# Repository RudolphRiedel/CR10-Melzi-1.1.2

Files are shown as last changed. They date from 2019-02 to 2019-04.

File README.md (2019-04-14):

This is a fork from https://github.com/Creality3DPrinting/CR10-Melzi-1.1.2

The files that Creality3D provided are neither the Source or Open and as a clone of the Melzi design which is under GPL Creality3D
should have released the real files over a year earlier than the subset that they released now.
Furthermore all Creality3D does is dumping the files on Github and not supporting them in any way.
All issues with the data seem to be ignored as well as any request.

Their supplied "CR-10 Schematic.pdf" does neither match the "CR-10 Motherboard.PCB" file,
nor is it the source-file but merely a picture.
For example, the controller is named U5 in the schematic but U8 in the board-file.
And the jumper J5 from the schematic to switch VCC between USB and the 5V regulator, it does not even exist
in the board-file.
Yes, there is an issue open for that: https://github.com/Creality3DPrinting/CR-10/issues/1

So, why the fuss, why this repository?
I still do care about the repairabilty of my CR-10 and Ender-3.

So I did my own version of the schematic from scratch based on the Ender-3.PCB in the Ender-3 repository.
This is my try to provide data for the V1.1.2 board as I believe Creality3D should have provided themselves when starting to sell the CR-10 at least.

This is a complete Altium Designer project now, saved with AD17.
Note: the "CR-10 Motherboard.PcbDoc" is not the same as "CR-10 Motherboard.PCB", it is based on that file but already
has a couple of bugfixes implemented. Not to change anything, but to correct the faulty patched mess of the "CR-10 Motherboard.PCB".

I would have loved to work on this together with Creality3D but I can only guess that they are not interested in really embracing open source. 

When I received my first Ender-3 it had a board installed in it with "V1.1.3" printed on the silkscreen.
I asked in the Ender-3 repository what changed from "V1.1.2" but got no answer to that quesion.

I am still not sure but I believe the only difference is that the header EXT-A2 has been replaced with a 100µF/16V capacitor.

The Ender-3 at least has been quietely been "upgraded" to a "V1.1.4" revision of the controller-board.
I only had pictures to work with but the only change that I found is that the FT232RL has been swapped out for a CH340G.
I find that is a bold move given that the USB chip provides the 3.3V for the SD-card and while the FT232RL is rated for 50mA, the CH340G does not even have a rating for the output current in the datasheet.
I would have added a small LDO for the 3.3V in addition but Creality3D did not.

I would not be surprised at all if this turns out to be a major cause for broken V1.1.4 boards.

Next thing I learned is that Creality3D started to offer a silent upgrade mainboard.
What they did is to replace the A4988 stepper drivers with TMC2208.
This is just a drop-in replacement and they did not change the board for it.
Also if you did receive your Ender-3 with a V1.1.4 board you likely have A4988 drivers installed.
Looking at a still from a Youtube video they changed the sense resistors from 0,1R to 0,15R.
C10, C14, C18 and C22 should have been changed to 22nF.

Original content of the README.md:

# CR10-Melzi-1.1.2
The CR10 Melzi 1.1.2 3D Printer Motherboard is now fully Open Source Hardware Association Certified.

UID:CN000004
https://certification.oshwa.org/list.html

Hardware and software licensed under the GPL v3 license, documentation licensed under CC BY-SA 4.0 International license.

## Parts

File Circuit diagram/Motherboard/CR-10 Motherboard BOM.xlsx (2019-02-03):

Quantity | Designator | Description | Comment | Footprint
1 | U2 | 74HC541 - Octal buffer/line driver | HC541 | SSOP-20
4 | U3, U4, U6, U7 | A4988 | A4988 | QFP28
1 | U8 | AVR 8-Bit, 128k FLASH, TQFP44 | ATMEGA1284P-AU | QFP-44
6 | C1, C2, C3, C4, C28, C30 | Capacitor Polarized | 100uF | CAP-100
1 | CP2 | Capacitor Polarized | 22uF | RVT4X5.5
1 | C45 | Chip Capacitor | 330nF | 0603
2 | C25, C40 | Chip Capacitor | 220nF | 0603
2 | C41, C42 | Chip Capacitor | 1uF | 0603
2 | C50, C51 | Chip Capacitor | 22p | 0603
25 | C10, C11, C12, C13, C14, C15, C16, C17, C18, C19, C20, C21, C22, C23, C24, C32, C33, C34, C35, C36, C37, C38, C39, C43, C44 | Chip Capacitor | 100nF | 0603
1 | C31 | Chip Capacitor | 100nF | 0805
5 | C5, C6, C7, C8, C9 | Chip Capacitor | 4.7uF | 0805
1 | CP1 | Chip Capacitor | 0.1uF | C0603
1 | CP3 | Chip Capacitor | 150pF | C0603
2 | R25, R26 | Chip Resistor | 1k | 0603
1 | 1k | Chip Resistor | R1-1 | 0603
12 | R18, R27, R28, R29, R30, R31, R32, R33, R34, R35, R36, R37 | Chip Resistor | 0R | 0603
16 | R1, R2, R3, R4, R5, R10, R11, R12, R14, R15, R17, R20, R21, R23, R24, R38 | Chip Resistor | 10k | 0603
4 | R13, R16, R19, R22 | Chip Resistor | 100k | 0603
4 | R6, R7, R8, R9 | Chip Resistor | 20k | 0603
1 | FP1 | Chip Resistor | 1.5A | MF-MSMF050
1 | R_P2 | Chip Resistor | 24.9k | R0603
1 | R_P4 | Chip Resistor | 210k | R0603
1 | R_P5 | Chip Resistor | 40.2k | R0603
3 | R_P1, R_P3, R_P6 | Chip Resistor | 100k | R0603
3 | JS1, JS2, JS3 | Chip Resistor | not populated | R10
8 | S1, S2, S3, S4, S5, S6, S7, S8 | Chip Resistor | 0.1R | R100
1 | 16M | Crystal HC49/US | 16Mhz | CRY
1 | DP1 | Diode | B340A-13-F | D-SMA
1 | DP2 | Diode | SS12 | D-SMA
3 | Fid1, Fid2, Fid3 | Fiducial | Fiducial | Fiducial-A
1 | U1 | FTDI USB UART I.C. | FT232RL | PL2303
7 | B-MOT, ETEMP, FAN, FAN1, X-STOP, Y-STOP, Z-STOP | Header 1x2 | XH2.54-2A | P2
1 | EXT-A2 | Header 1x3 | XH2.54-3A | XH-3A
4 | E-MOT, X-MOT, Y-MOT, Z-MOT | Header 1x4 | XH2.54-4A | P4
1 | ISP | Header 2x3 | HEADER 3X2
1 | EXP1 | Header 2x5 | Header 2x5 | SOP10
1 | LP1 | Inductor | 15uH/3A | DO3316P
2 | LED1, LED2 | LED | blue | 0603
1 | TF | microSD | TF | TF
1 | UP1 | MP1584 | MP1584 | SOIC8E
3 | M1, M2, M3 | N-FET | REP30N06LE | TO-252
4 | RP1, RP2, RP3, RP4 | RTrimm | 10k | RP
3 | Hotbed, Hotend, PWR | Terminal 1x2 | HP128-5.0-2P | MOT-2
1 | USB | USB | mini-USB | USB

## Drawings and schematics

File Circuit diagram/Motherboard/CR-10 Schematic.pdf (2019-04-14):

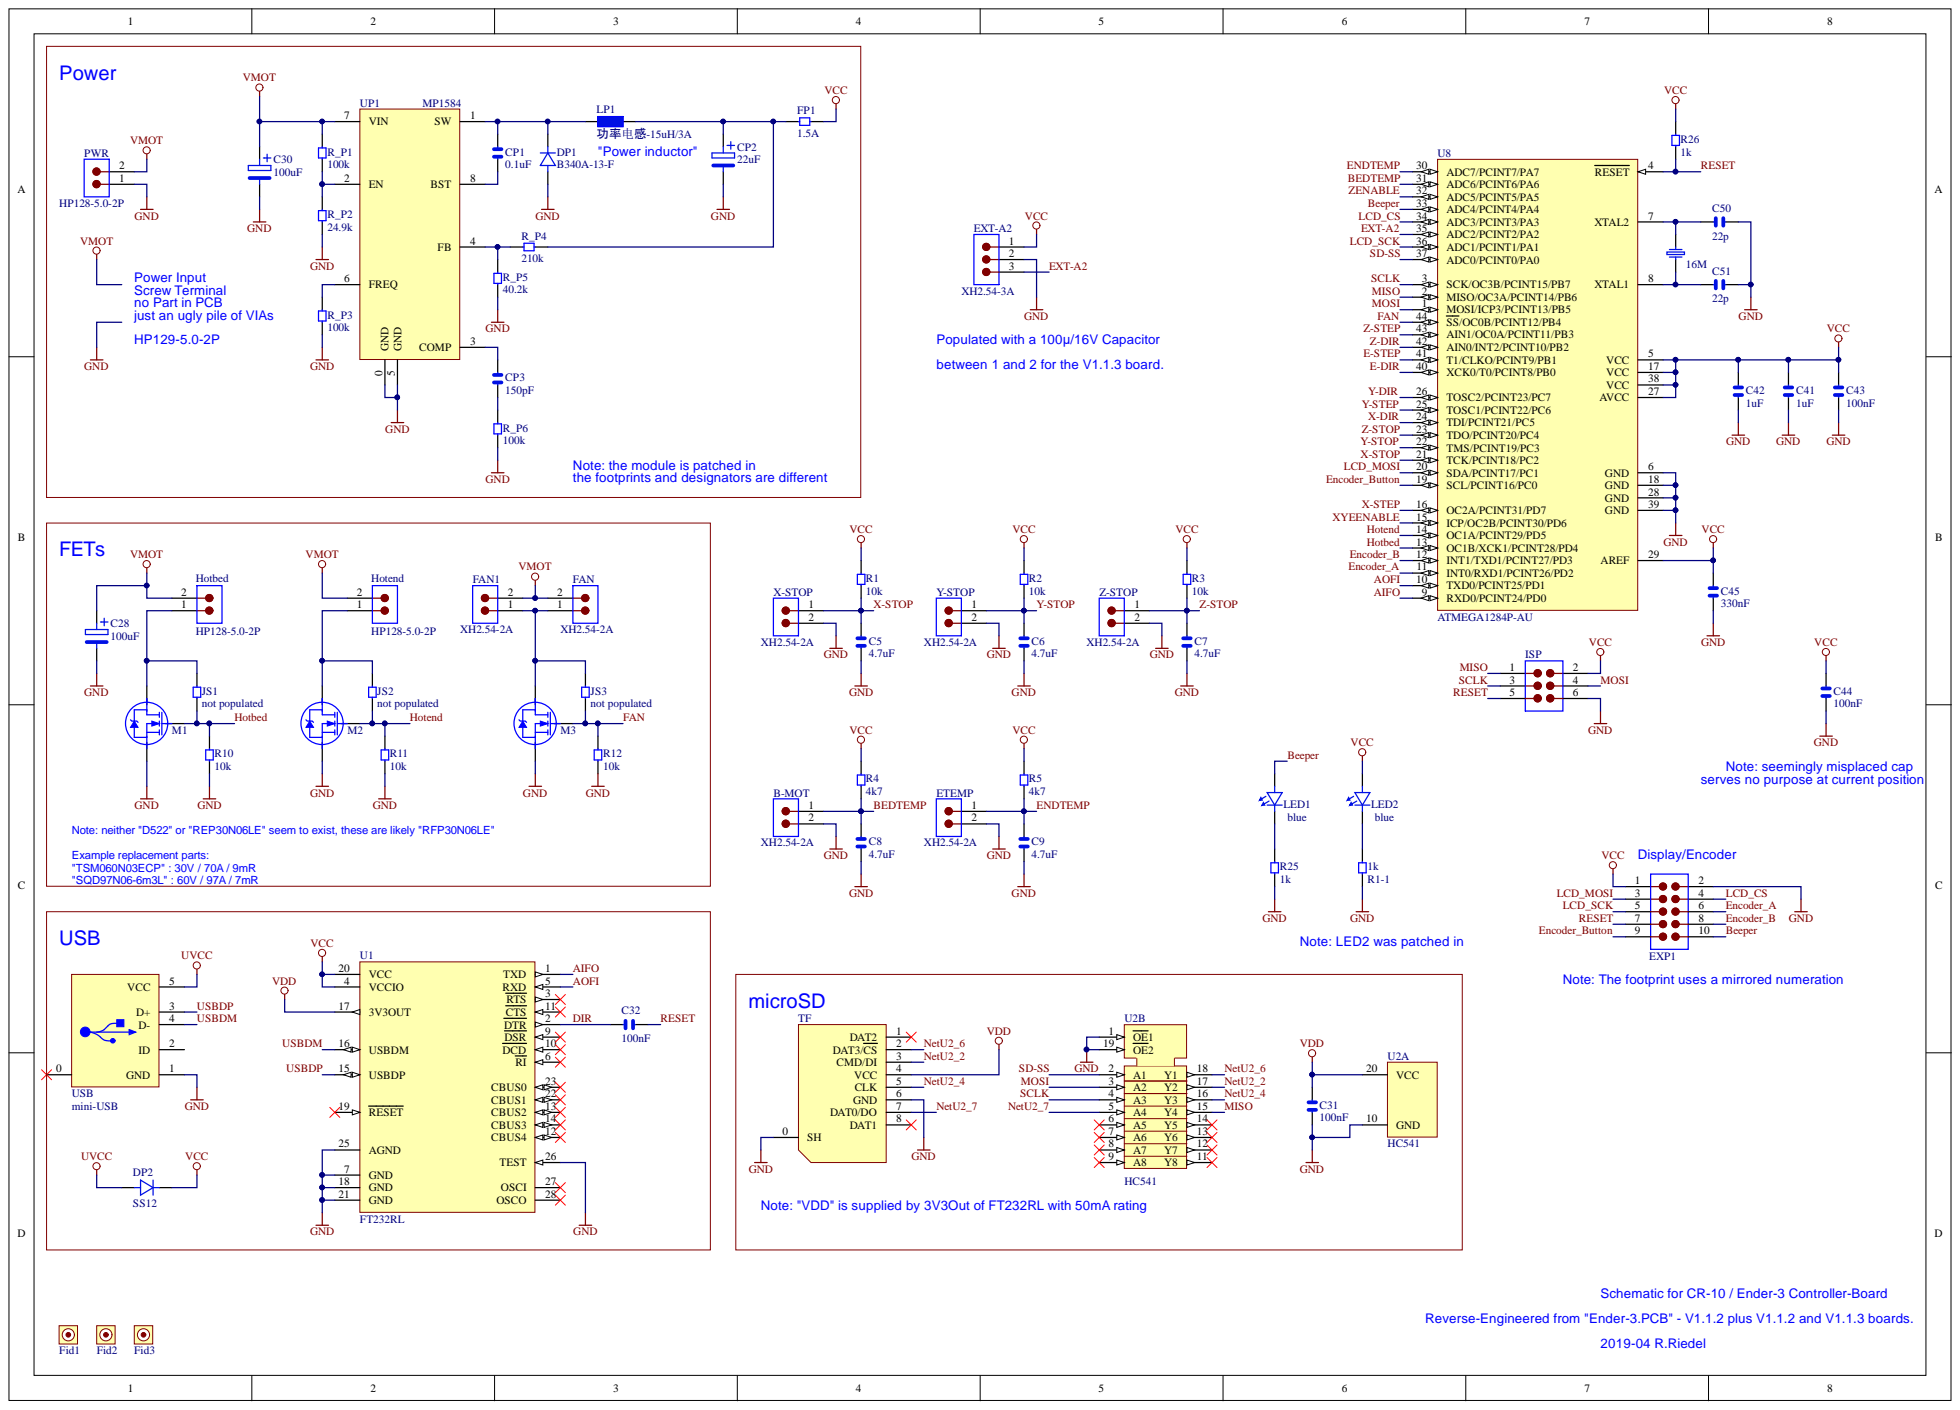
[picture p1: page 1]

Power Input
Screw Terminal no Part in PCB

just an ugly pile of VIAs

between 1 and 2 for the V1.1.3 board.

Note: the module is patched in
the footprints and designators are different

serves no purpose at current position Note: seemingly misplaced cap

Note: neither "D522" or "REP30N06LE" seem to exist, these are likely "RFP30N06LE"

GND
Note: LED2 was patched in

Note: The footprint uses a mirrored numeration

GND 7

GND 21

Note: "VDD" is supplied by 3V3Out of FT232RL with 50mA rating

Schematic for CR-10 / Ender-3 Controller-Board

Reverse-Engineered from "Ender-3.PCB" - V1.1.2 plus V1.1.2 and V1.1.3 boards.

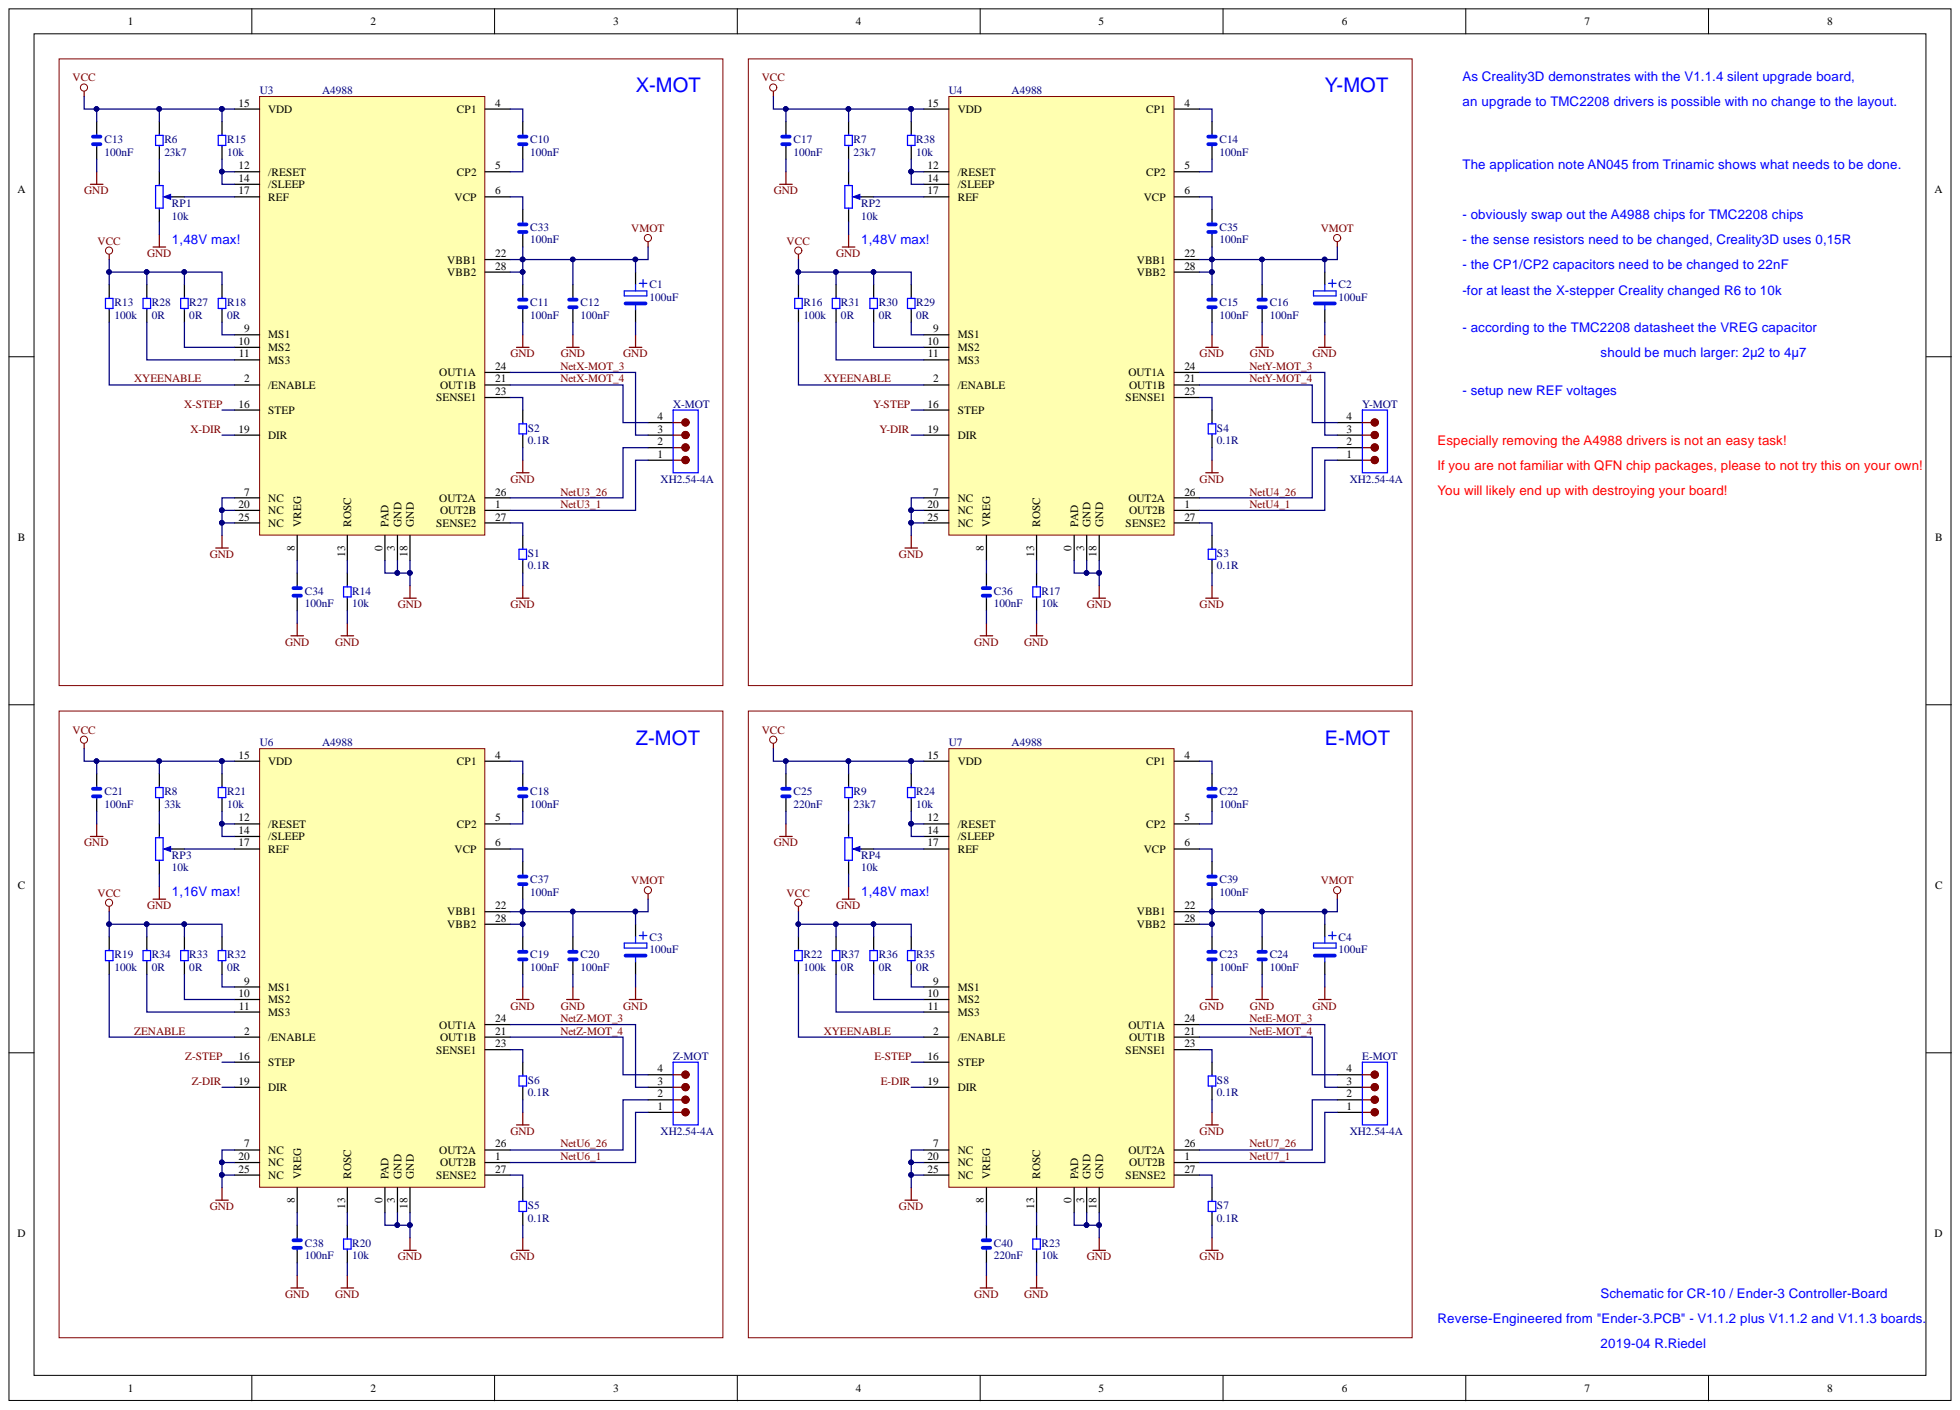
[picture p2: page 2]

As Creality3D demonstrates with the V1.1.4 silent upgrade board,

an upgrade to TMC2208 drivers is possible with no change to the layout.

The application note AN045 from Trinamic shows what needs to be done.

- obviously swap out the A4988 chips for TMC2208 chips

- the sense resistors need to be changed, Creality3D uses 0,15R

- the CP1/CP2 capacitors need to be changed to 22nF

-for at least the X-stepper Creality changed R6 to 10k

- according to the TMC2208 datasheet the VREG capacitor

should be much larger: 2µ2 to 4µ7

- setup new REF voltages

Especially removing the A4988 drivers is not an easy task!

If you are not familiar with QFN chip packages, please to not try this on your own!

You will likely end up with destroying your board!

Schematic for CR-10 / Ender-3 Controller-Board

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

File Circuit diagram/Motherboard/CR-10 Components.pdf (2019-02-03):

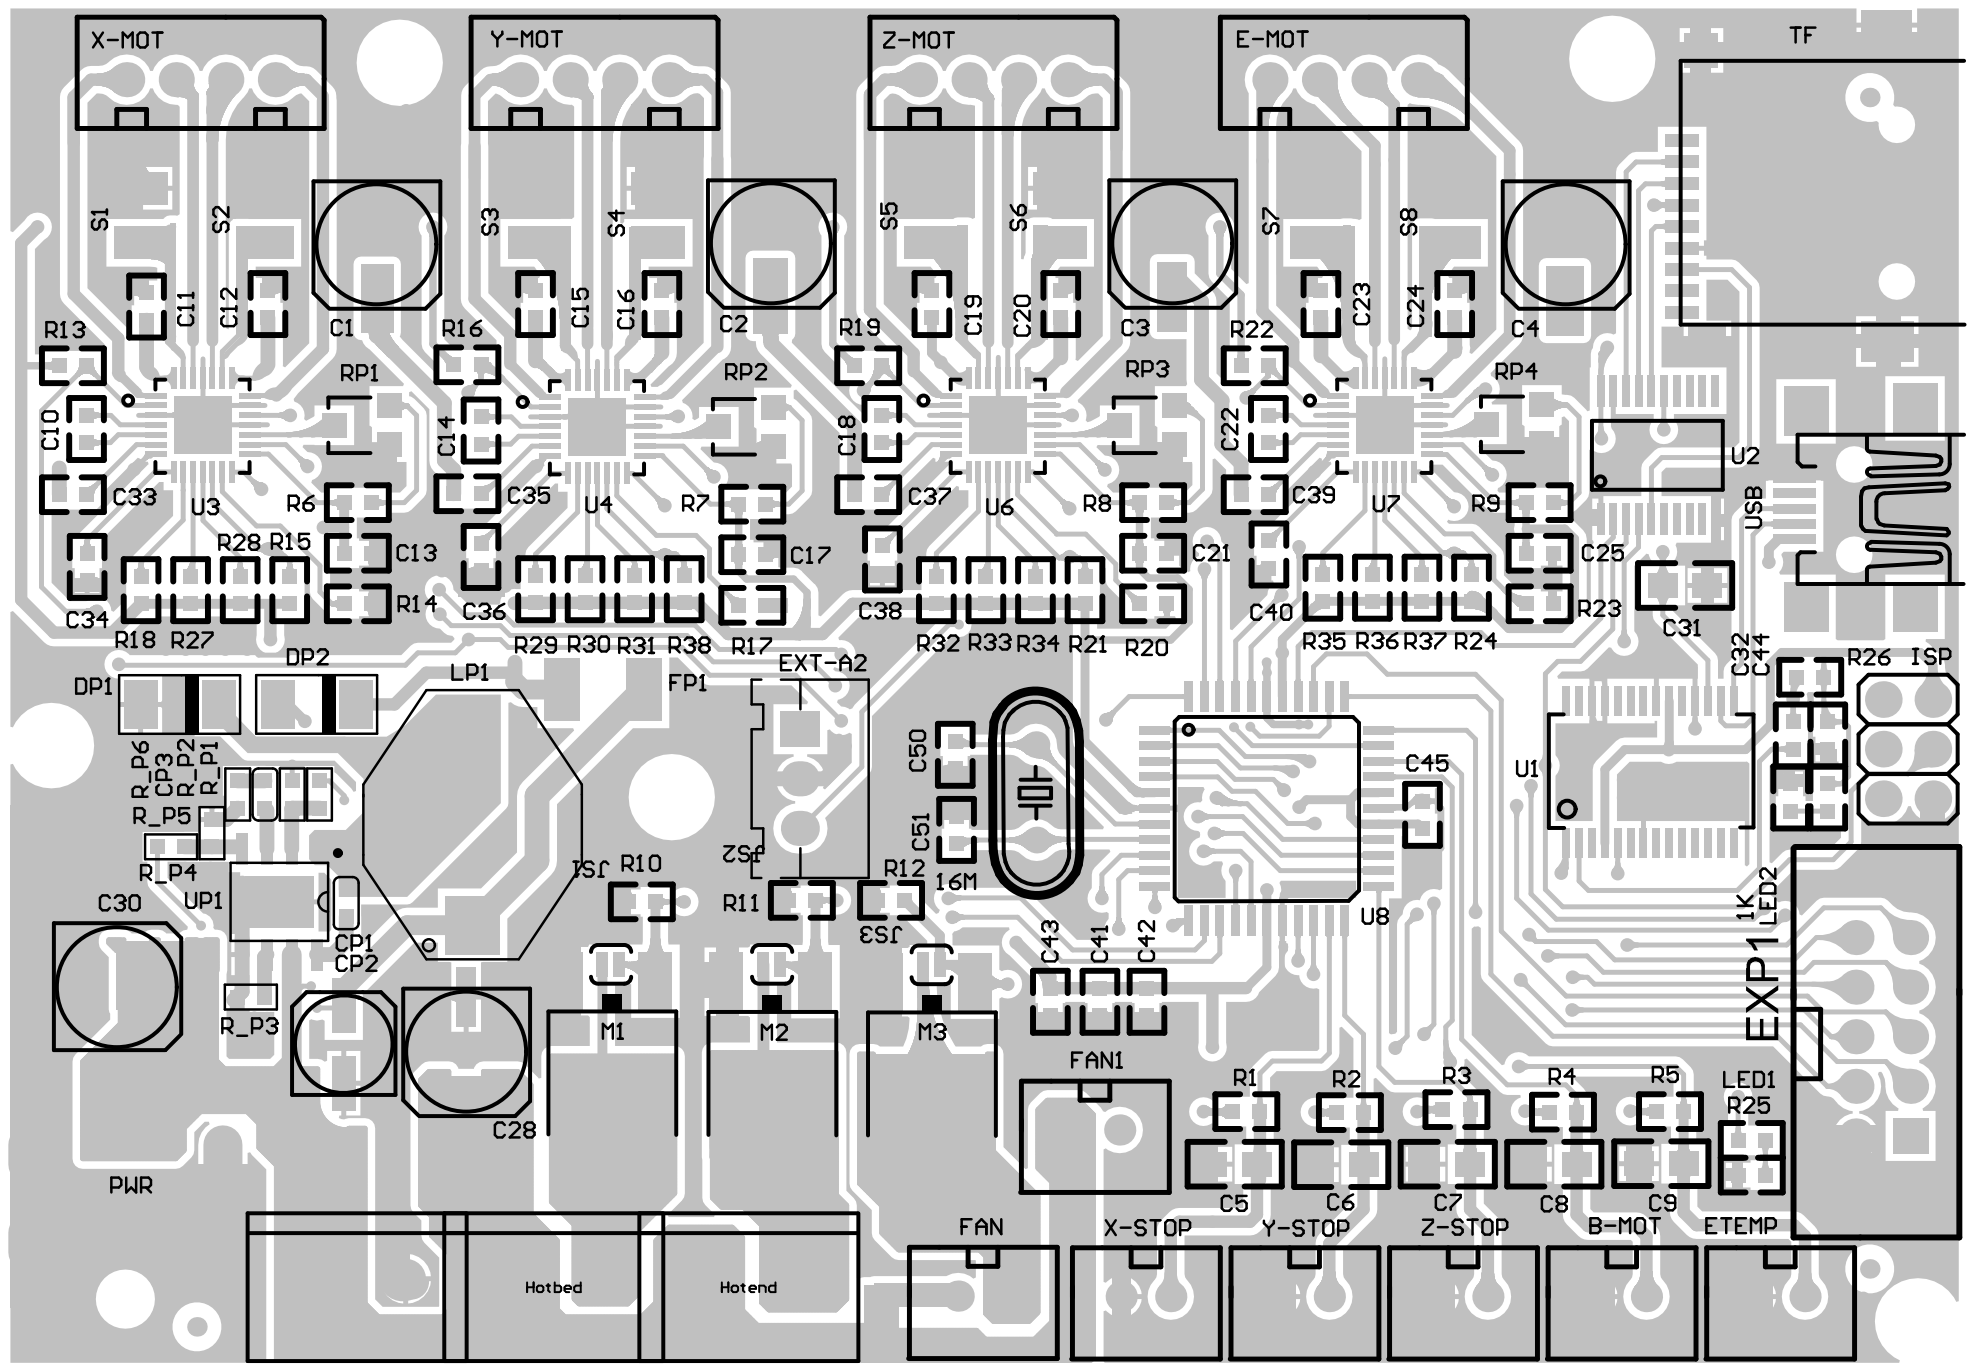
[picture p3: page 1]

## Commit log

2019-01-27 Remove duplicated directory
    [Configuration.h, Configuration_adv.h, Menu Plans.xlsx]
2019-02-03 many more fixes to the original data
    [CR-10 Motherboard BOM.xlsx, CR-10 Motherboard.PcbDoc, CR-10 Motherboard.PrjPcb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]
2019-04-14 - went over V1.1.2 and V1.1.3 boards with an USB microscope and corrected a few resistor values to what is actually populated on the boards - compared images of the front- and back-sides of the V1.1.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
    [CR-10 Motherboard.PcbDoc, CR-10 Motherboard_1.SchDoc, CR-10 Motherboard_2.SchDoc]
